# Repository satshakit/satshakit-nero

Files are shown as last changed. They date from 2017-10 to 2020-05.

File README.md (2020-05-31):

<h1 style="font-family: courier;" align="center"> satshakit-nero</h1>
<p align="center">
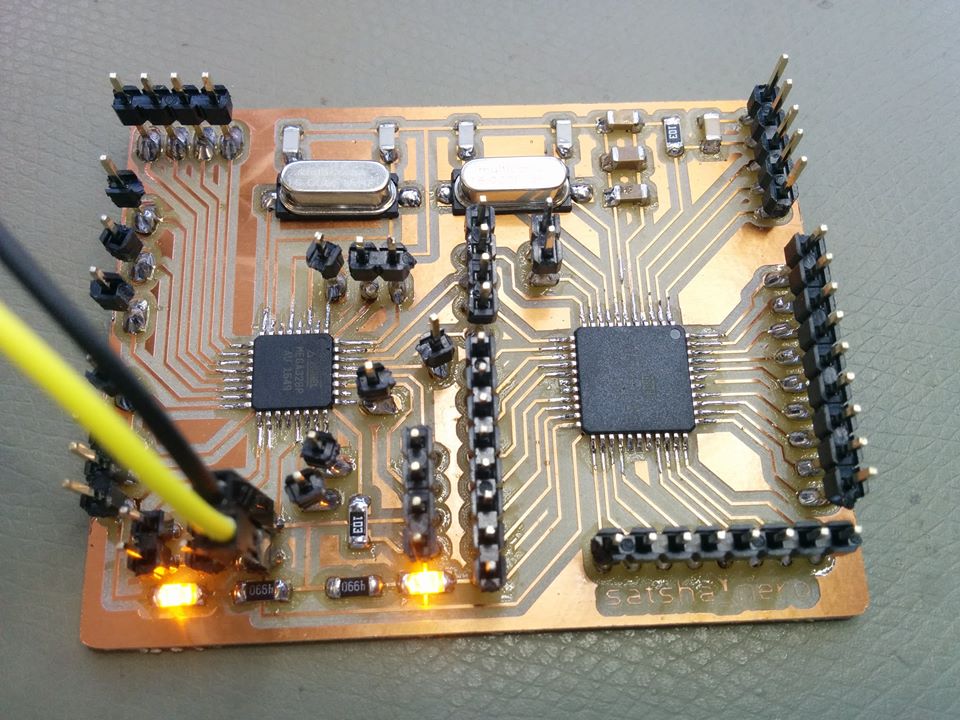
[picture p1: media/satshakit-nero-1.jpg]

<div align="center"><i>An improved & fabbable multi-mcu flight controller board.</i></div>
</p>  

What is satshakit?
--

satshakit is a **Arduino IDE  and libraries compatible**, fabbable and open source board.

Here you can find all of the satshakit boards: **[satshakit organization](https://github.com/satshakit)**.

satshakit-nero
--

**satshakit-nero** is microcontroller board designed around the **ATMega1284P** and the **ATMega328P** chips and it is suitable for advanced drone applications and scenarios in which it is needed to have two available microcontrollers. The ATMega328P manages the flight with the **[Multiwii](http://www.multiwii.com/)** while the ATMega1284P can be used to inject and override the transmitter stick values (ROLL, PITCH, YAW and THROTTLE) or to manage a set of additional sensors. In the board there is a jumper to enable or disable the serial communication between the two microcontrollers (SERIAL_COMMON in the Eagle board).

The ATMega328P microntroller gives to this board all the features of the original **[satshakit flight controller board](https://github.com/satshakit/satshakit-flight-controller)**:

- support for [any drone configuration](http://www.multiwii.com/connecting-elements) up to **8 motors**
- support for up to **6 channels** receivers 
- **16mhz crystal** for precise clock, reliability and compatibility
- possibility to connect and use **any IMU working at 5V** 

And plus it adds the features of the **[satshakit-128](https://github.com/satshakit/satshakit-128)**:

- **128k** flash memory
- **2 serials**
- **16k of ram**
- **32 IO** pins

Here you can have a look on **satshakit-nero board**:

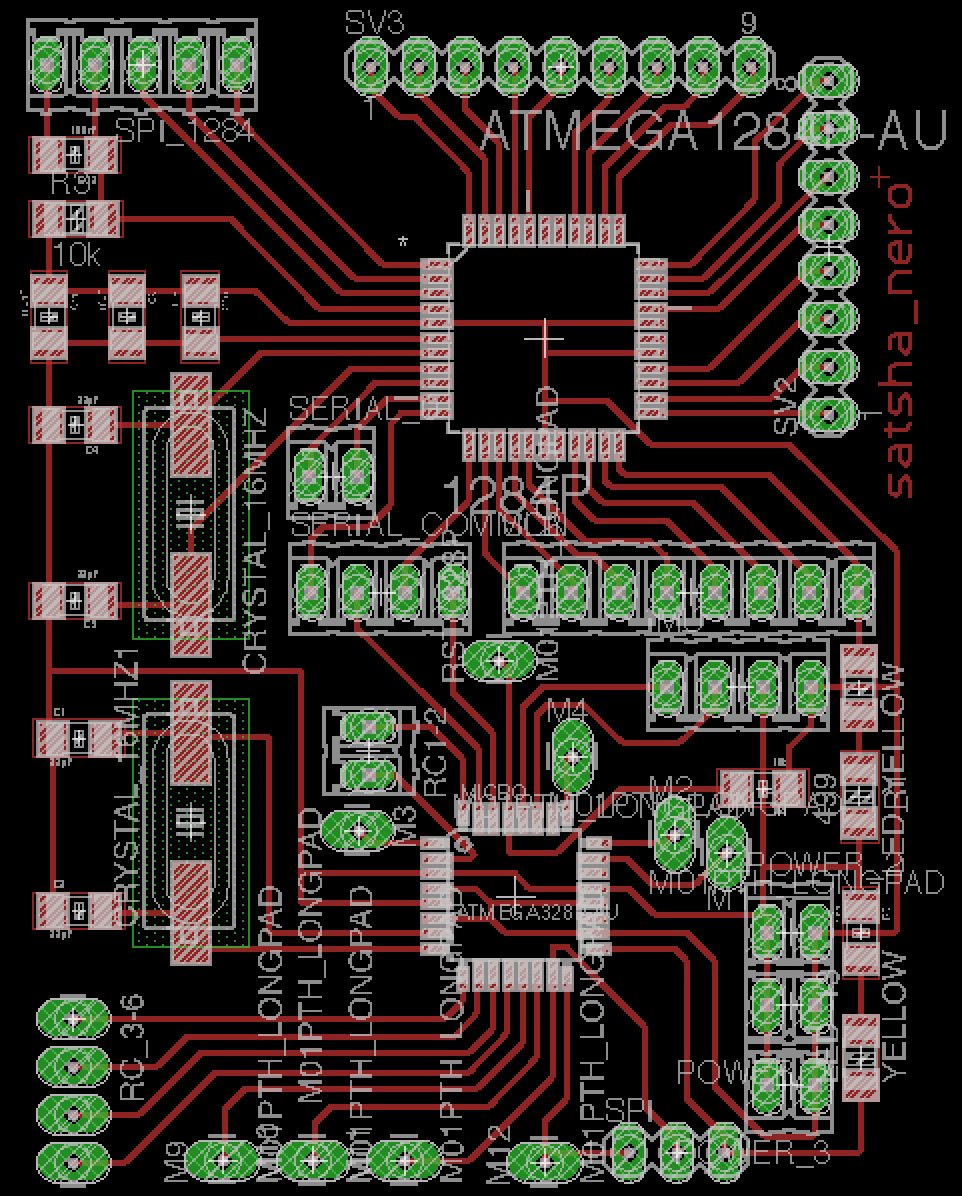
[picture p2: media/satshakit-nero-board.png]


**downloads (right click, download as)**

- [satshakit-nero eagle schematic](https://raw.githubusercontent.com/satshakit/satshakit-nero/master/eagle/satshakit-nero/satshakit-nero.sch)
- [satshakit-nero eagle board](https://raw.githubusercontent.com/satshakit/satshakit-nero/master/eagle/satshakit-nero/satshakit-nero.brd)
- [satshakit-nero inside cut png](https://raw.githubusercontent.com/satshakit/satshakit-nero/master/media/satshakit-nero-inside.png)
- [satshakit-nero outsite cut png](https://raw.githubusercontent.com/satshakit/satshakit-nero/master/media/satshakit-nero-outside.png)

**media**

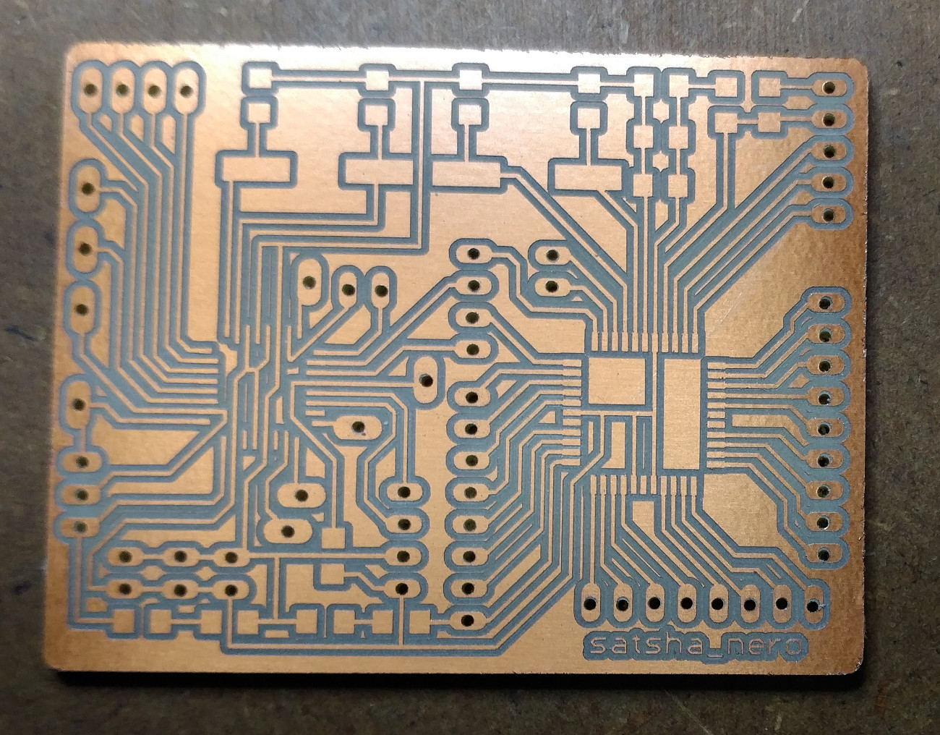
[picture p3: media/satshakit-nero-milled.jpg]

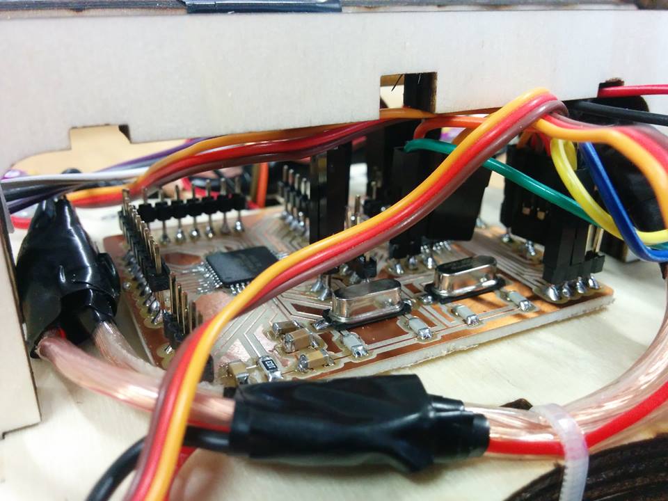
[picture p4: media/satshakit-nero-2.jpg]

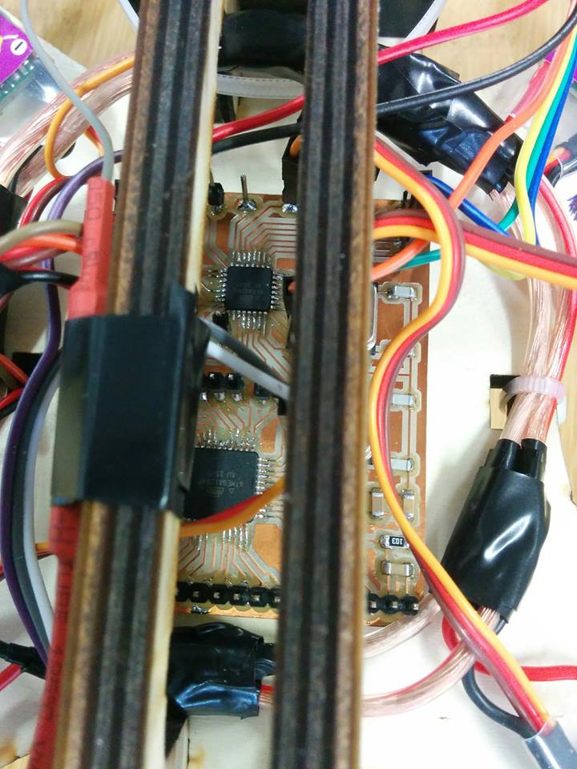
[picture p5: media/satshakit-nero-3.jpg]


satshakit-nero flying test:

<a href="http://www.youtube.com/watch?feature=player_embedded&v=5o7xKqsNKFE
" target="_blank"></a>

Authors
--

- Daniele Ingrassia

Contact
--

- **ingrassiada@gmail.com**
- **[linkedin](http://it.linkedin.com/in/danieleingrassia)**

Thanks
--

[Aldo Sollazzo and Noumena.io](http://noumena.io/)

[Fablab Kamp-Lintfort](http://fablab.hochschule-rhein-waal.de/index.php/de/)<br />
Hochschule Rhein-Waal<br />
Friedrich-Heinrich-Allee 25, 47475 Kamp-Lintfort, Germany<br />
fablab@hochschule-rhein-waal.de

License
--
This work is licensed under the terms of the open source license: Creative Commons Attribution-ShareAlike 4.0 International ([CC BY-SA 4.0](https://creativecommons.org/licenses/by-sa/4.0/)).

Disclaimer  
--

<div class="align-justify">
This hardware/software is provided "as is", and you use the hardware/software at your own risk. Under no circumstances shall any author be liable for direct, indirect, special, incidental, or consequential damages resulting from the use, misuse, or inability to use this hardware/software, even if the authors have been advised of the possibility of such damages.</div>

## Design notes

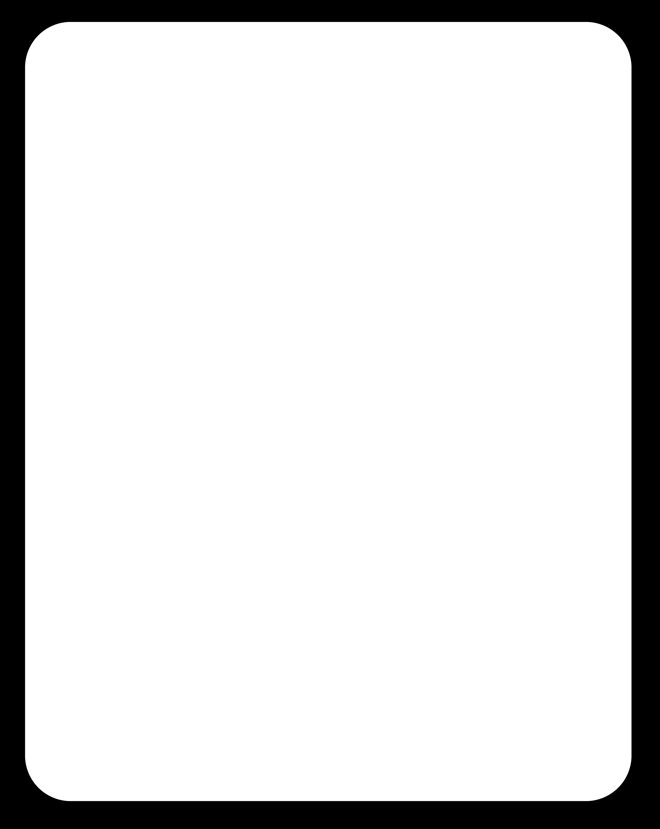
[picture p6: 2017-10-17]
media/satshakit-nero-outside.png

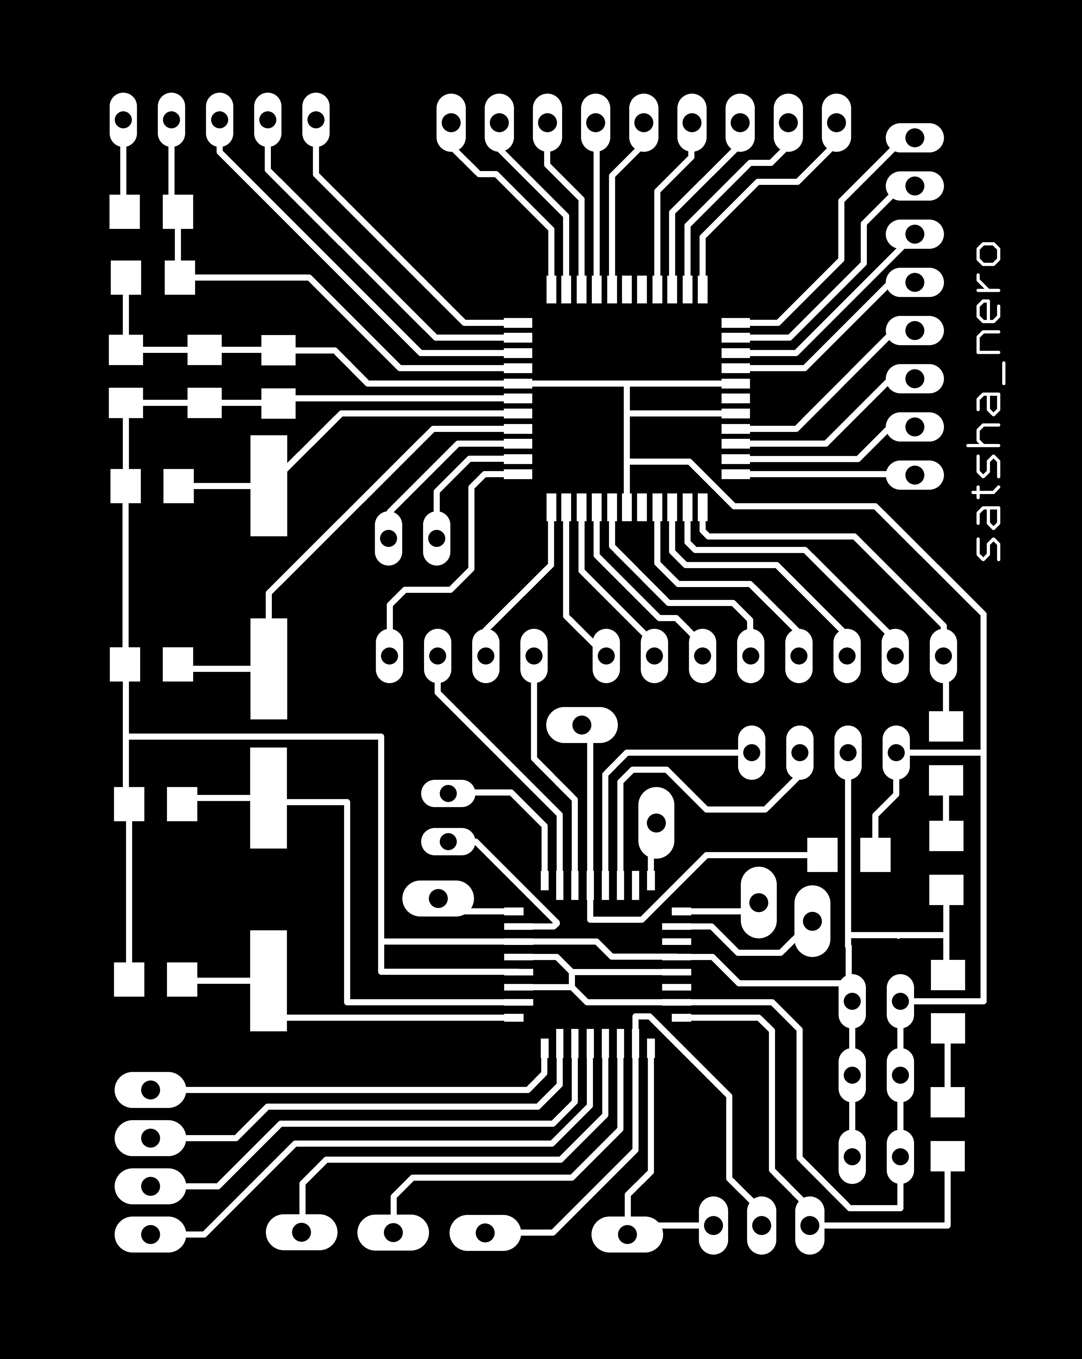
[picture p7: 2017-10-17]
media/satshakit-nero-inside.png

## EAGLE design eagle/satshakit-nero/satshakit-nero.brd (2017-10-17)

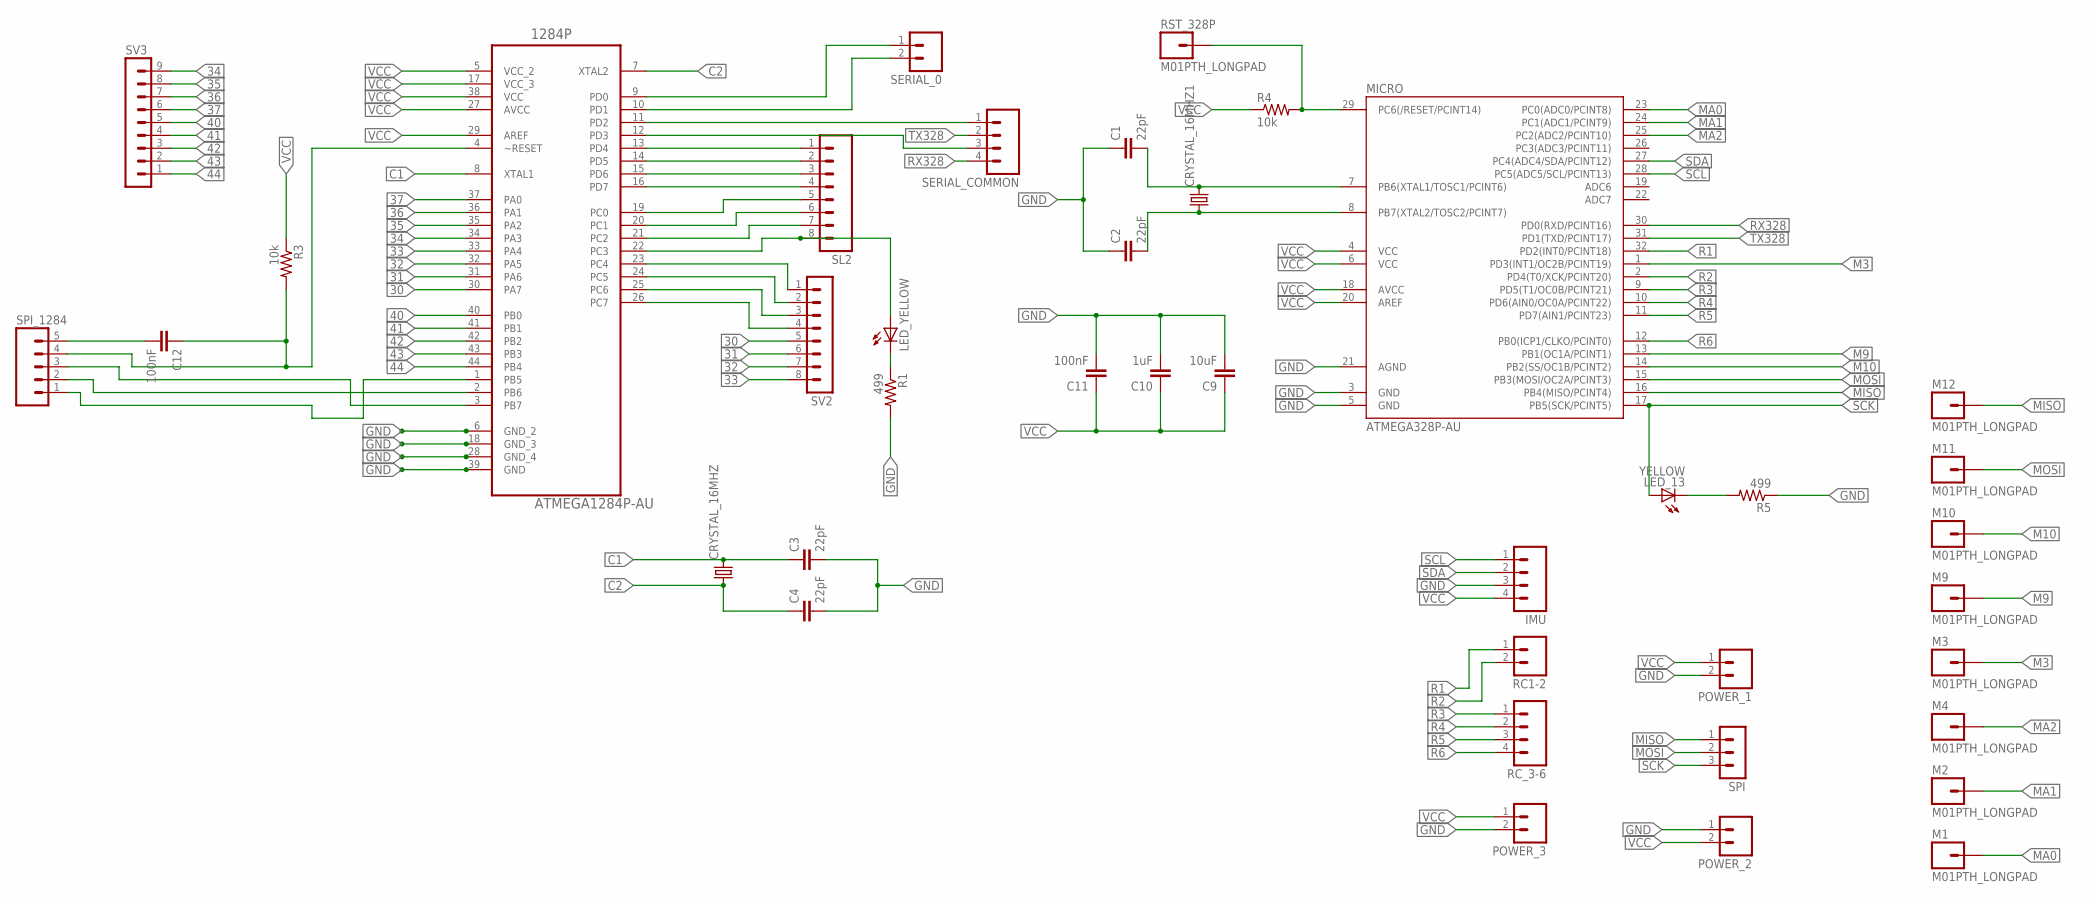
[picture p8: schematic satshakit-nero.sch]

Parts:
1284P: ATMEGA1284P-AU; QFP80P1200X1200X120-44N
C1, C2, C3, C4: 22pF; 1206
C9: 10uF; 1206
C10: 1uF; 1206
C11, C12: 100nF; 1206
CRYSTAL_16MHZ, CRYSTAL_16MHZ1: CRYSTALHC49UP; HC49UP
IMU: M04; 04P
LED_13: YELLOW; 1206
LED_YELLOW: LED1206; 1206
M1, M2, M3, M4, M9, M10, M11, M12: M01PTH_LONGPAD; 1X01_LONGPAD
MICRO: ATMEGA328P-AU; TQFP32-08
POWER_1, POWER_2, POWER_3: M02; 02P
R1: 499; R1206
R3: 10k; R1206
R4: 10k; 1206
R5: 499; 1206
RC1-2: M02; 02P
RC_3-6: M04LONGPADS; 1X04_LONGPADS
RST_328P: M01PTH_LONGPAD; 1X01_LONGPAD
SERIAL_0: M02; 02P
SERIAL_COMMON: M04; 04P
SL2: M08; 08P
SPI: MA03-1
SPI_1284: M05; 05P
SV2: MA08-1
SV3: MA09-1

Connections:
30: 1284P.30 (PA7), SV2.5
31: 1284P.31 (PA6), SV2.6
32: 1284P.32 (PA5), SV2.7
33: 1284P.33 (PA4), SV2.8
34: 1284P.34 (PA3), SV3.9
35: 1284P.35 (PA2), SV3.8
36: 1284P.36 (PA1), SV3.7
37: 1284P.37 (PA0), SV3.6
40: 1284P.40 (PB0), SV3.5
41: 1284P.41 (PB1), SV3.4
42: 1284P.42 (PB2), SV3.3
43: 1284P.43 (PB3), SV3.2
44: 1284P.44 (PB4), SV3.1
C1: 1284P.8 (XTAL1), C3.1, CRYSTAL_16MHZ.2
C2: 1284P.7 (XTAL2), C4.1, CRYSTAL_16MHZ.1
GND: 1284P.6 (GND_2), C1.1, C2.1, C3.2, C4.2, C9.2, C10.2, C11.2, IMU.3, MICRO.3 (GND), MICRO.5 (GND), MICRO.21 (AGND), POWER_1.2, POWER_2.1, POWER_3.2, R1.2, R5.1
M3: M3.1, MICRO.1 (PD3(INT1/OC2B/PCINT19))
M9: M9.1, MICRO.13 (PB1(OC1A/PCINT1))
M10: M10.1, MICRO.14 (PB2(SS/OC1B/PCINT2))
MA0: M1.1, MICRO.23 (PC0(ADC0/PCINT8))
MA1: M2.1, MICRO.24 (PC1(ADC1/PCINT9))
MA2: M4.1, MICRO.25 (PC2(ADC2/PCINT10))
MISO: M12.1, MICRO.16 (PB4(MISO/PCINT4)), SPI.1
MOSI: M11.1, MICRO.15 (PB3(MOSI/OC2A/PCINT3)), SPI.2
unnamed: 1284P.19 (PC0), SL2.5
unnamed: 1284P.20 (PC1), SL2.6
unnamed: 1284P.16 (PD7), SL2.4
unnamed: 1284P.14 (PD5), SL2.2
unnamed: 1284P.13 (PD4), SL2.1
unnamed: 1284P.12 (PD3), SERIAL_COMMON.3
unnamed: 1284P.11 (PD2), SERIAL_COMMON.1
unnamed: 1284P.9 (PD0), SERIAL_0.1
unnamed: 1284P.10 (PD1), SERIAL_0.2
unnamed: 1284P.21 (PC2), SL2.7
unnamed: 1284P.22 (PC3), LED_YELLOW.1 (A), SL2.8
unnamed: 1284P.23 (PC4), SV2.1
unnamed: 1284P.24 (PC5), SV2.2
unnamed: 1284P.25 (PC6), SV2.3
unnamed: 1284P.26 (PC7), SV2.4
unnamed: 1284P.15 (PD6), SL2.3
unnamed: 1284P.3 (PB7), SPI_1284.3
unnamed: 1284P.2 (PB6), SPI_1284.2
unnamed: 1284P.1 (PB5), SPI_1284.1
unnamed: 1284P.4 (~RESET), C12.1, R3.2, SPI_1284.4
unnamed: LED_YELLOW.2 (C), R1.1
unnamed: C12.2, SPI_1284.5
unnamed: C1.2, CRYSTAL_16MHZ1.2, MICRO.7 (PB6(XTAL1/TOSC1/PCINT6))
unnamed: C2.2, CRYSTAL_16MHZ1.1, MICRO.8 (PB7(XTAL2/TOSC2/PCINT7))
unnamed: MICRO.29 (PC6(/RESET/PCINT14)), R4.2, RST_328P.1
unnamed: LED_13.2 (C), R5.2
R1: MICRO.32 (PD2(INT0/PCINT18)), RC1-2.1
R2: MICRO.2 (PD4(T0/XCK/PCINT20)), RC1-2.2
R3: MICRO.9 (PD5(T1/OC0B/PCINT21)), RC_3-6.1
R4: MICRO.10 (PD6(AIN0/OC0A/PCINT22)), RC_3-6.2
R5: MICRO.11 (PD7(AIN1/PCINT23)), RC_3-6.3
R6: MICRO.12 (PB0(ICP1/CLKO/PCINT0)), RC_3-6.4
RX328: MICRO.30 (PD0(RXD/PCINT16)), SERIAL_COMMON.4
SCK: LED_13.1 (A), MICRO.17 (PB5(SCK/PCINT5)), SPI.3
SCL: IMU.1, MICRO.28 (PC5(ADC5/SCL/PCINT13))
SDA: IMU.2, MICRO.27 (PC4(ADC4/SDA/PCINT12))
TX328: MICRO.31 (PD1(TXD/PCINT17)), SERIAL_COMMON.2
VCC: 1284P.5 (VCC_2), 1284P.17 (VCC_3), 1284P.27 (AVCC), 1284P.29 (AREF), C9.1, C10.1, C11.1, IMU.4, MICRO.4 (VCC), MICRO.6 (VCC), MICRO.18 (AVCC), MICRO.20 (AREF), POWER_1.1, POWER_2.2, POWER_3.1, R3.1, R4.1

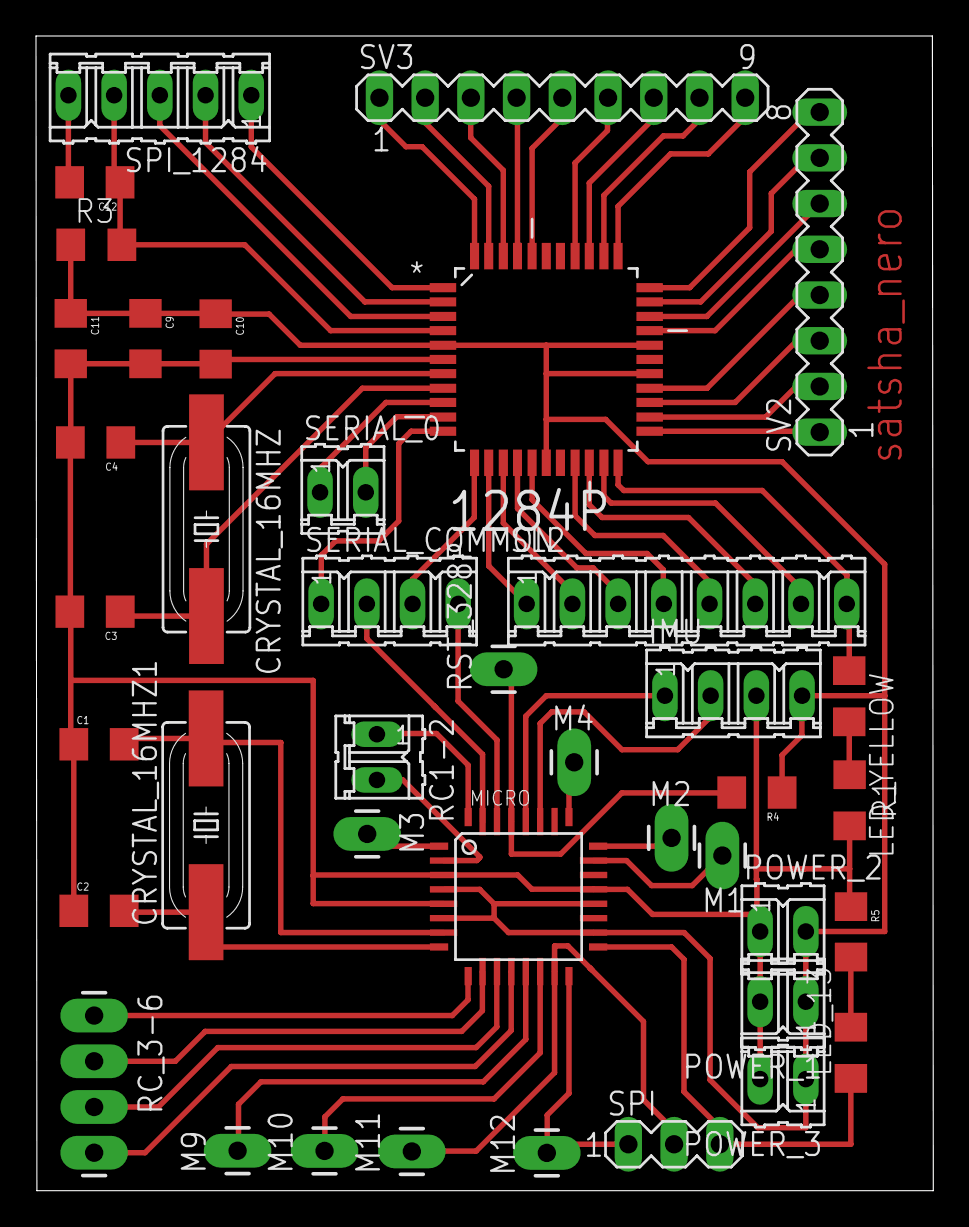
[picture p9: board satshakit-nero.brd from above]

Board: 2 copper layers, 49.8 x 64.1 mm, 40 parts (0 on the bottom side), 62 nets.

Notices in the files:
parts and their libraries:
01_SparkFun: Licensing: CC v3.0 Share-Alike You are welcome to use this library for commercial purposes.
